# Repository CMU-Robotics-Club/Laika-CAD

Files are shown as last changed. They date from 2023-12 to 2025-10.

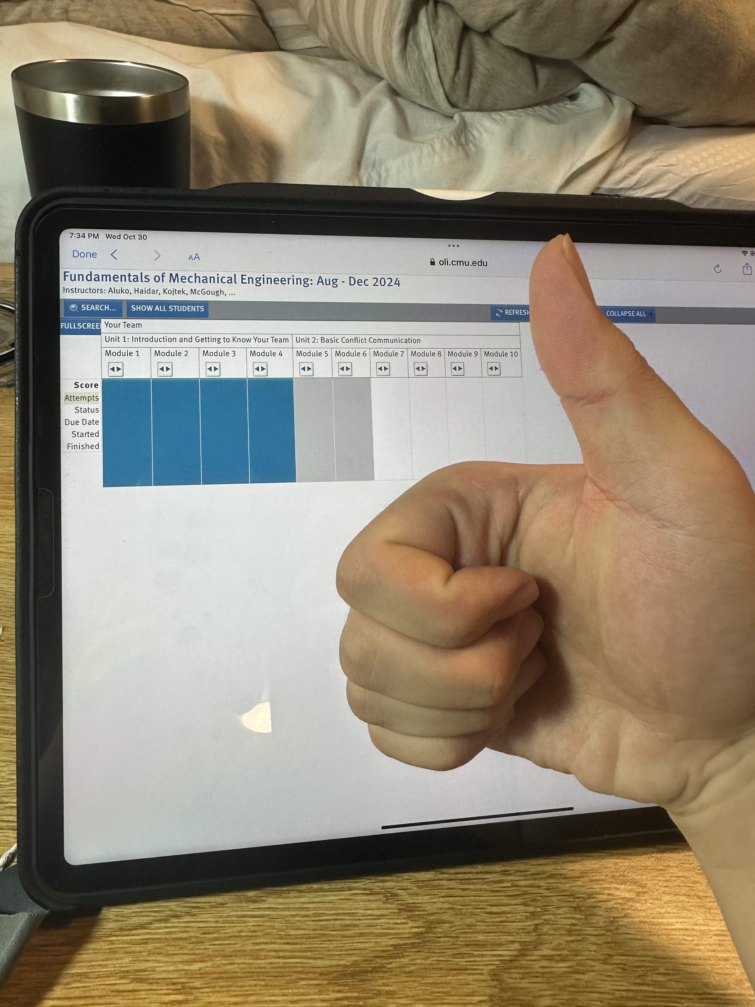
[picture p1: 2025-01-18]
LEG/IMG_3947.jpg

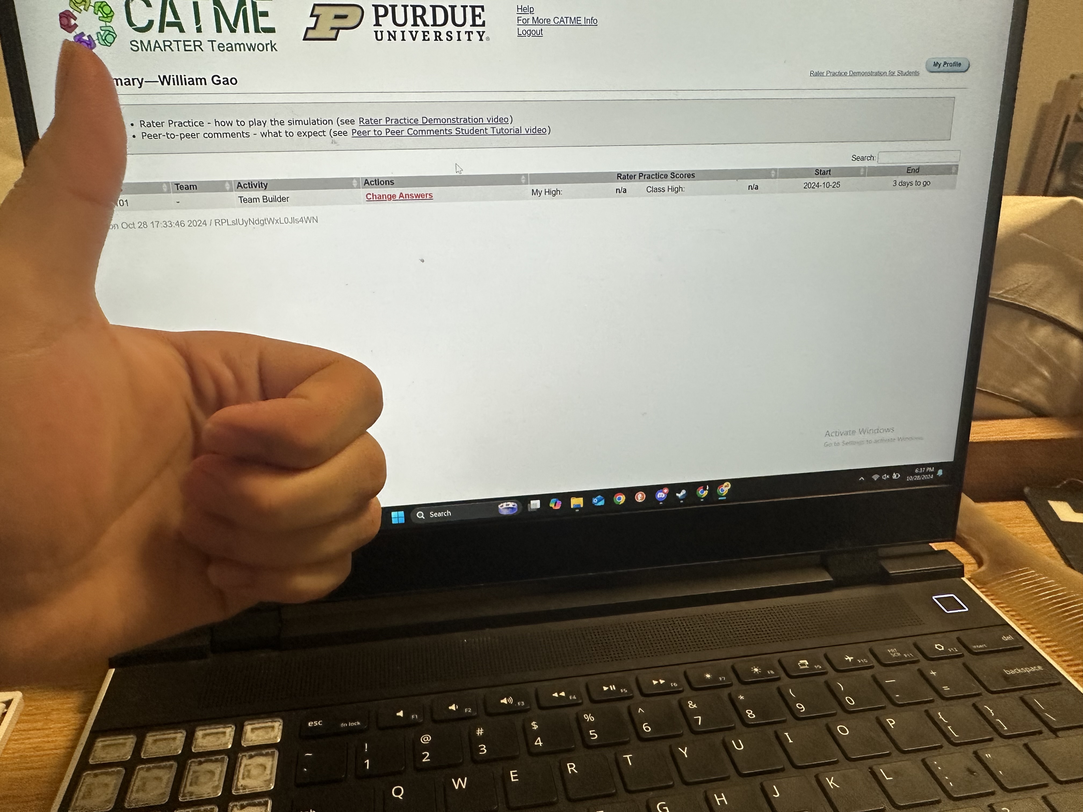
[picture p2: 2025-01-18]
LEG/IMG_3941.jpg

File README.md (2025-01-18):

# Laika-CAD
 Quadruped Project CAD Repo

## 1: Description
This repo contains all the CAD for the CMU Robotics Club Quadrupeds Project. All CAD files, whether for the robot itself, a prototype, test structures, unused designs, or anything else should live within this repo. The CAD software of choice is SOLIDWORKS; non-SOLIDWORKS files should ideally be converted when possible or clearly marked with their respective software if conversion is problematic. The overall structure follows National Robotics Engineering Center EPDM standards as detailed below.

## 2: File Locations
The top level of CAD should only contain file folders and the top-level full assembly. Folders are created for submodules (legs, drivetrain, chassis, etc.) and for component types. COTS (Commercial Off-The-Shelf) components should be identified in a COTS folder; if generic enough to have application in multiple submodules, they should live in top-level COTS. The top-level COTS includes subdirectories for component types (fasteners, bearings, etc.). If a subdirectory appropriate for a part does not exist, create one. Note that these subdirectories should have more within them (for example, a FASTENERS subdir should contain BOLTS, NUTS and NUTS should contain NYLOC, PEM, JAM) If the COTS component is highly specific, should exist in lower level COTS folder in submodule directory. Files should generally be separated by file classifiers (see below). Top-level submodule directories should only contain 900-level files and 200-level files that belong to no subassembly. 200-level files which are part of subassemblies should be organized into descriptive subdirectories. All other file levels should be organized into subdirectories within the submodule directory (e.g. a simulation for a drive train motor shaft should be within a SIMULATION folder placed in the same directory as the top-level assembly for the drive train submodule). 000, 100, 400 series files should live within MANUFACTURING, DRAWINGS, and SIMULATION folders respectively placed within the same directory as the subassembly to which the relevant parts belong to.

## 3: File Naming
### 3.1: Custom
Custom parts should obey the XXXX YZZ - NAME file number convention:  
XXX: Module ID (Alphabetical)   
Y: File type classifier (Numbers)   
ZZ: Part number (Numbers)   
NAME: Descriptive file name in Title Capitalization Form     

Example:
CYC 208 - Gearbox Mount Plate

The Module ID is an up-to-four-character code that describes the module the file belongs to. Should be as descriptive as four characters allow. The list of current module classifiers can be seen below:  
LAIK: Top-level assembly  
CHAS: Chassis  
DRIV: Drive train  
CYC: Cycloidal gearbox  
LEG: Leg design  
MTST: Motor test rig  
LTST: Leg test rig  

Please maintain this list as the project scope evolves.

The file type classifiers are as follows:  
0: Manufacturing file formats (STL, DXF, GCODE, etc.)  
1: Drawings  
2: Individual parts  
3: Equation .txt files  
4: Solidworks FEA Simulation Files  
5: Jigs/tools related to the assembly/manufacture of another part  
6: Weldments  
7: Piping, tubing, wiring, related  
8: Subassemblies  
9: Top-level assemblies. Typically no more than one (plus configurations) per module  

Please update this list as the scale of the project evolves.  

Part numbers should be defined beginning at 01. Number parts as they are created regardless of complexity, dependency, etc. Ensure that each part number for a given file type is only used once per subassembly. If you have more than 99 parts in a subassembly, you are doing something wrong!

Example:  
The completed drive train assembly would be named DRIV-901 - Drive Train Assem and would exist in the top-level DRIVE TRAIN folder.  
The housing subassembly would be DRIV-801 - Drive Train Housing and would exist in the lower-level DRIVE TRAIN/HOUSING folder.  
The drawing for one of the housing components would be DRIV-105 - Drive Train Top Cover and would exist in the DRIVE TRAIN/DRAWINGS folder.

### 3.2: COTS
COTS (Commercial Off-The-Shelf) parts should be named descriptively but do not need original part numbers. McMaster parts can be left as named when exporting as SLDPRT. Non-McMaster parts should be named descriptively, typically including part type, key dimensions, material as appropriate, etc. Additionally, should include manufacturer and part number. Use your best judgement! Someone with no project experience should be able to, from the file name, tell what the part is and where to order it.

### 3.3: Directories

Directories should be named in ALL CAPS. They should be named to describe the subassembly, component type, etc.

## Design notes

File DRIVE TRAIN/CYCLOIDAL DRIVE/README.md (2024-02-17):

# Gearbox info

Reduction: 14:1

Eccentricity: 1mm

Pin Diameter: 6mm

Pin Circle Diameter: 75mm

# List of COTS used
## Bearings
Flanged Ultra-Thin Ball Bearing with Steel Ring, Shielded, for 15 mm Shaft Diameter, 4 mm Wide - 2x
- [McMaster](https://www.mcmaster.com/4390N165/)

Flanged Ultra-Thin Ball Bearing with 440C Stainless Steel Ring, Shielded, for 10mm Shaft Diameter, 4mm Wide -2 x
- [McMaster](https://www.mcmaster.com/4390N149/)

5909K22_Needle-Roller Thrust Bearing - 1x
-  Thrust bearing with 78mm OD, 55mm ID, and 3mm Thickness
-  [McMaster](https://www.mcmaster.com/5909K22/)

1 mm Thick Washer for 55 mm Shaft Diameter Needle-Roller Thrust Bearing
-  [Mcmaster](https://www.mcmaster.com/5909k82/)

## Fasteners - this is currently misinformation
M3x14 Socket Head - 5x
- Used to fasten the load pins to rotating plate

M3 nuts - 10x
- Used to fasten the load pins to roatating plate
- Used to give threaded attachment points to the rotating plate

M3x10 Socket Head - 3x
- Used to fasten lid to main housing

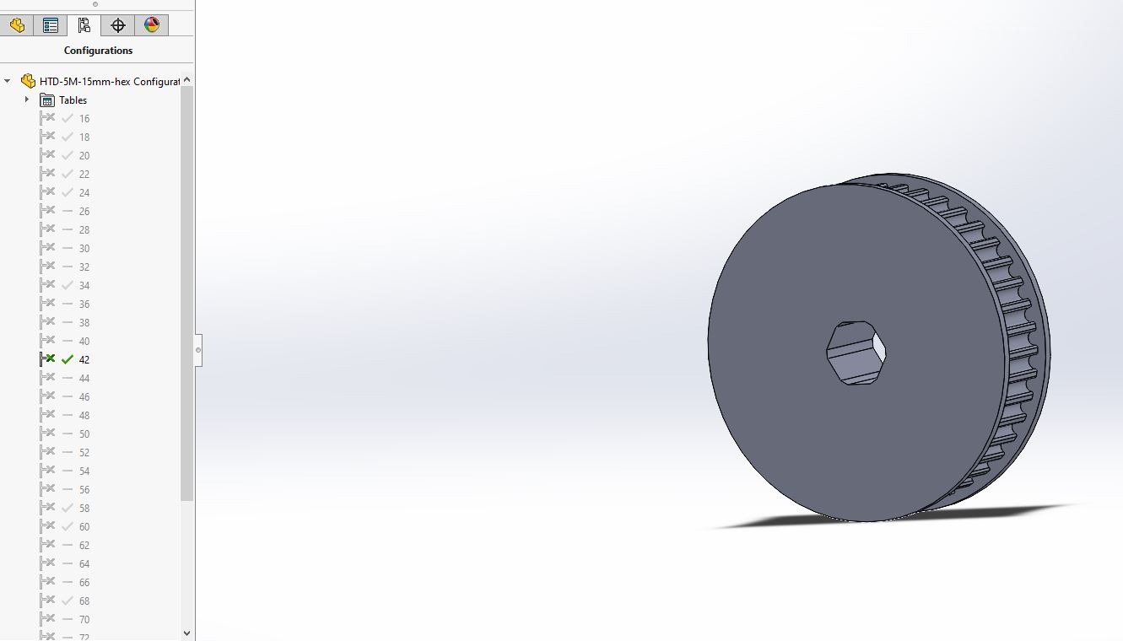
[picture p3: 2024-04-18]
PULLEY GEN/Pulley generator screenshot.JPG

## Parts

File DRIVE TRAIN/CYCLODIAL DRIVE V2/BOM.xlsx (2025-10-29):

Part Name | Description | Quantity needed per Gearbox | Total Quantitiy needed | Cost | per Unit | Total Price | Link
Shaft End Bearing | 18x12x4 Bearing | 2 | 24 | $9.99 | 10 | $29.97 | https://www.amazon.com/XIKE-6701-2RS-Bearings-12x18x4mm-Pre-Lubricated/dp/B09D2RQ4Y1
Shaft Bearing | 21x15x4 Bearing | 2 | 24 | $8.49 | 4 | $50.94 | https://www.amazon.com/uxcell-6702-2RS-Groove-Bearing-Bearings/dp/B0CNX3W3YB/ref=sr_1_11?sr=8-11
Disk Bearing | 17x9x5 | 12 | 144 | $9.99 | 10 | $149.85 | https://www.amazon.com/uxcell-9x17x5mm-Miniature-Lubricated-Bearings/dp/B0D6W6Z113/ref=sr_1_3?sr=8-3
Output Bearing | 72x55x9 | 1 | 12 | $9.99 | 2 | $59.94 | https://www.amazon.com/uxcell-6811ZZ-Groove-Bearings-Shielded/dp/B082PW8F3S/ref=sr_1_3?sr=8-3
M6 Threaded Output Pin | M6xM4x24 | 6 | 72 | $2.35 | 1 | $169.20 | https://www.mcmaster.com/97355A302/
M4 Output Pin Screws | M4 x 6mm | 6 | 72 | $7.19 | 120 | $7.19 | https://www.amazon.com/BNUOK-120pcs-Socket-Threads-Spanner/dp/B0DYS5W46C/ref=sr_1_3?sr=8-3
M3 Disk Screws | M3 x 5mm | 12 | 144 | $7.99 | 180 | $7.99 | https://www.amazon.com/BNUOK-180pcs-Socket-Threads-Spanner/dp/B0DJQGJGYT?sp_csd=d2lkZ2V0TmFtZT1zcF9hdGY
M3 Output Bearing Cover Screws | M3 x 10mm | 6 | 72 | $7.64 | 180 | $7.64 | https://a.co/d/bKohAkp
M3 Hull Screws | M3 x 50mm | 5 | 60 | $8.99 | 120 | $8.99 | https://a.co/d/6JlE1u1
Number of Gearboxes: | 12 |  |  |  | Total: | $491.71
 |  |  |  |  | Price per Gearbox: | $40.98

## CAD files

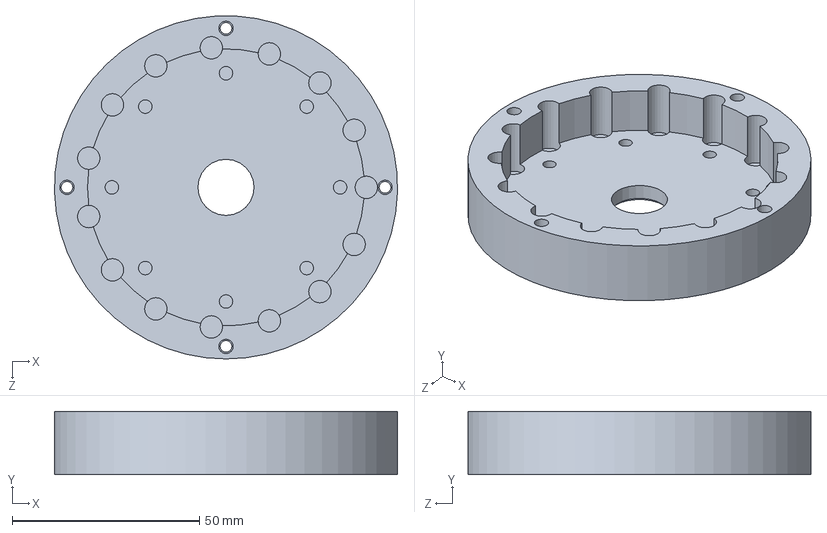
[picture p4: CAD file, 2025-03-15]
DRIVE TRAIN/CYCLOIDAL DRIVE/CYC 201 - Main Body.SLDPRT
91.7 x 16.9 x 91.6 mm

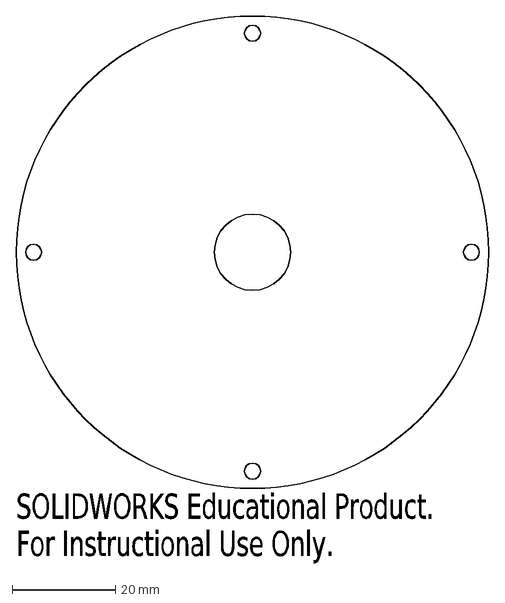
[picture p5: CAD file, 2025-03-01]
DRIVE TRAIN/CYCLOIDAL DRIVE/000 - LASER CUTTER FILES/CYC 001 - Main Body.DXF
SOLIDWORKS Educational Product.
For Instructional Use Only.

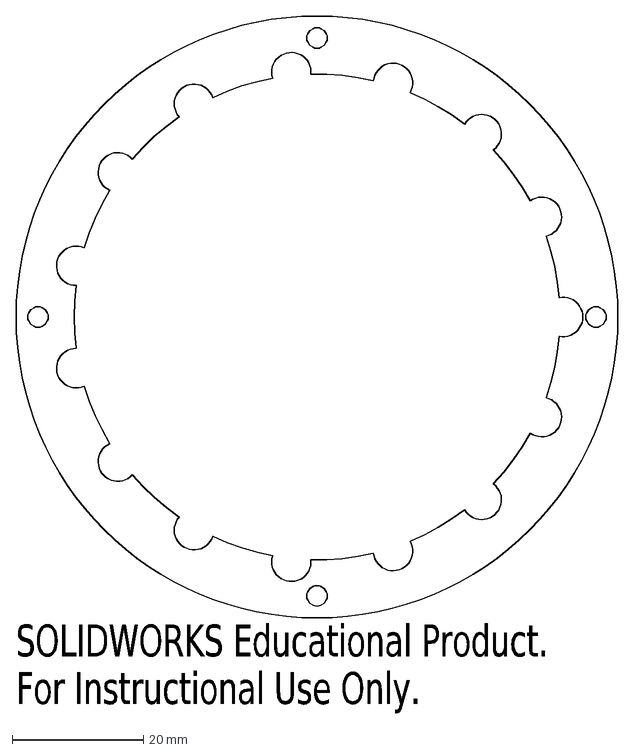
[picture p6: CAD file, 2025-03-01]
DRIVE TRAIN/CYCLOIDAL DRIVE/000 - LASER CUTTER FILES/CYC 002 - Main Body 2.DXF
SOLIDWORKS Educational Product.
For Instructional Use Only.

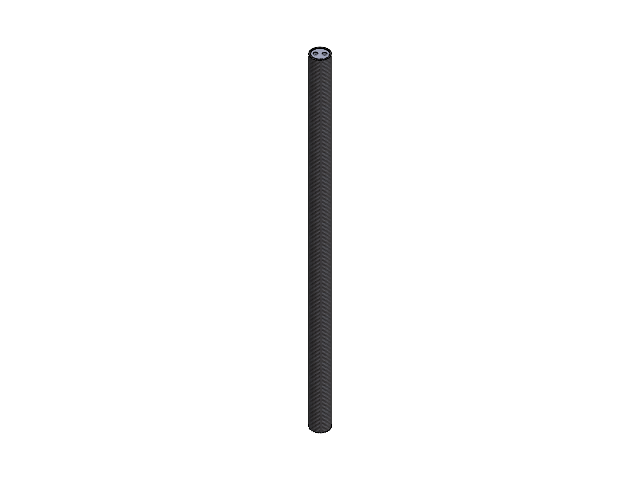
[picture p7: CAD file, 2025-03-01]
CHASSIS/CHA 804 - Middle Tube.SLDASM
CHA 202 - Middle Tube
tubePlug x 2

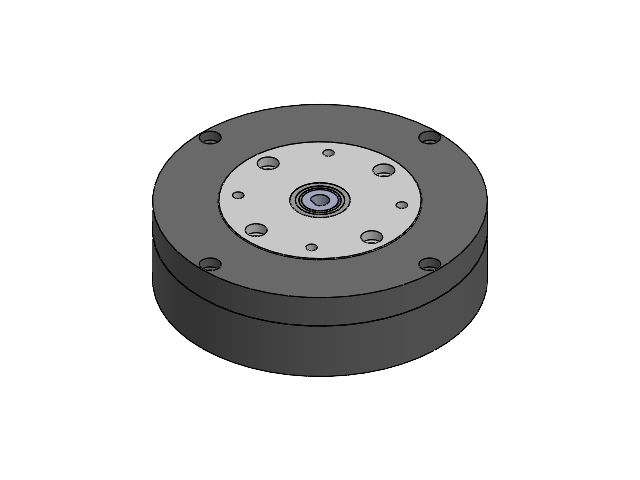
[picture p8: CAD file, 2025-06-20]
DRIVE TRAIN/CYCLOIDAL DRIVE/CYC 801 - Cycloidal Gearbox.SLDASM
CYC 205 - Eccentric Nut
CYC 204 - Eccentric Gear x 2
CYC 201 - Main Body
CYC 203 - Wall Pin x 15
CYC 207 - Top Hat
CYC 206 - Load Pin x 4
CYC 202 - Top Lid
5909K82_1 mm Thick Washer for 55 mm Shaft Diameter Needle-Roller Thrust Bearing x 2
5909K22_Needle-Roller Thrust Bearing(1)

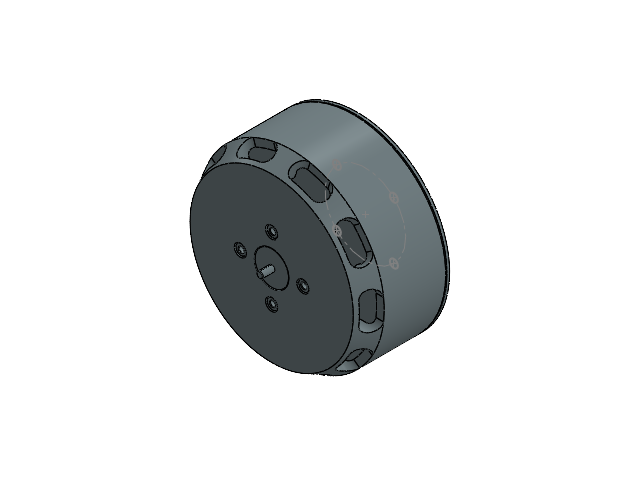
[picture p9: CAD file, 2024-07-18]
COTS - ODRIVE MOTOR/idk what all this is tbh/M8325S Motor v2.SLDASM
Magnet 5x5 Cylinder N45SH Diametrical
Saite 8325 120kv
Magnet Holder 8325 5mm

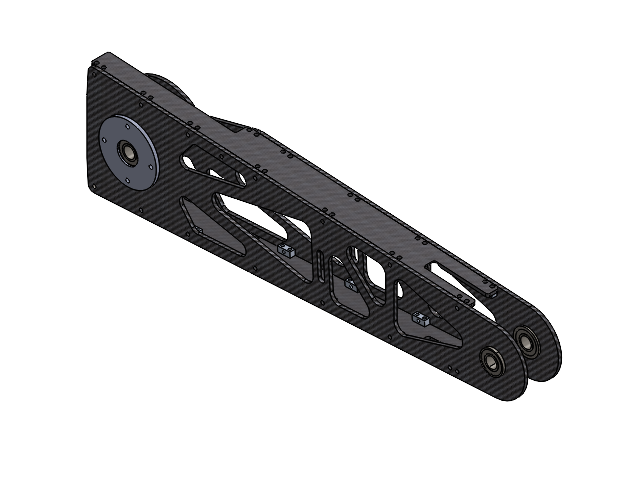
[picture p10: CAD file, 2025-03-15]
LEG/LEG 805 - Full Arm.SLDASM
LEG 213 - Arm Side Plate1
LEG 231 - LegCFSide
LEG 232 - LegCFSideDown
5mm_NutStrip_2x1_R1.1 x 25
LEG 233 - Arm Outer Plate
10.25mm Flanged Bearing.step x 3
Leg 235 - Hip Spacer
57155K629_Flanged Ball Bearing

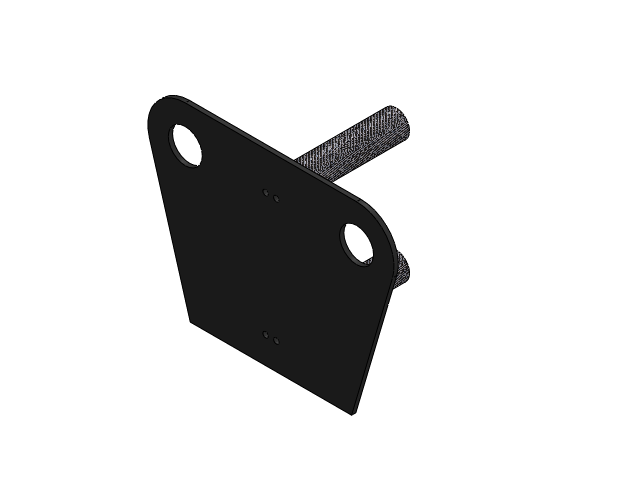
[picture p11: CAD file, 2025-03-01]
CHASSIS/CHA 802 - Front Assembly.SLDASM
CHA 203 - Front Plate
CHA 205 - Short Tube x 2
tubePlug x 4

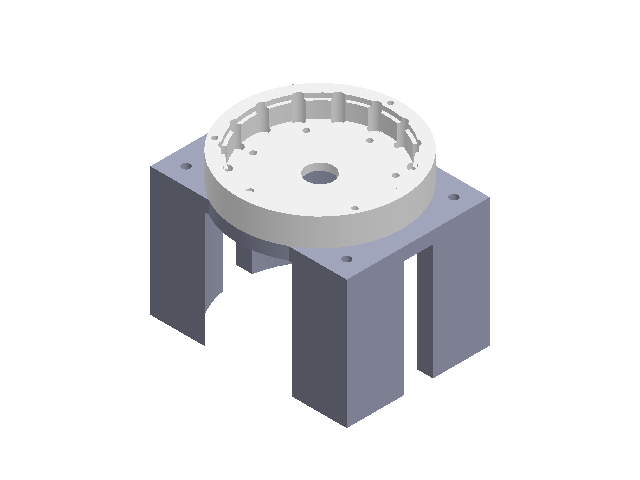
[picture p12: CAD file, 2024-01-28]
TEST RIG/GEARBOX TESTING/GTST-901 - TEST SETUP.SLDASM
GTST - 201
mainHousing

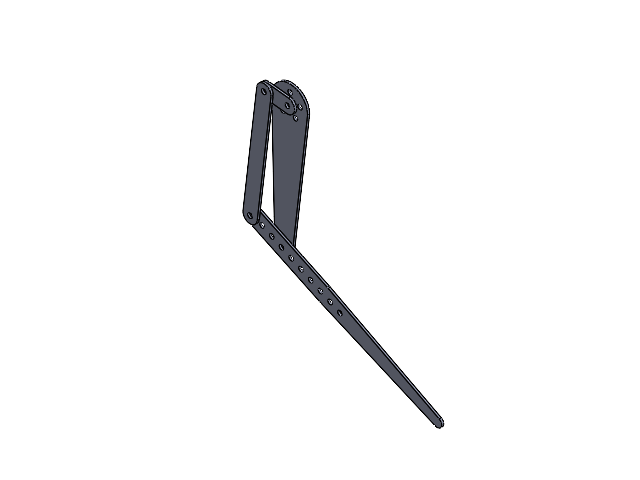
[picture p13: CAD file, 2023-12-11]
TEST RIG/LEG MODELING/LTST-901 - Test Rig.SLDASM
Upper leg
Lower leg
Shoulder flange
Tendon

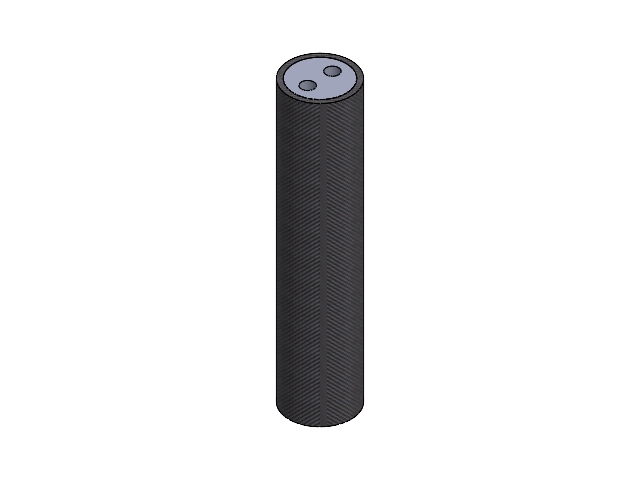
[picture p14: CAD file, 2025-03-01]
CHASSIS/CHA 805 - Short Tube.SLDASM
CHA 205 - Short Tube
tubePlug x 2

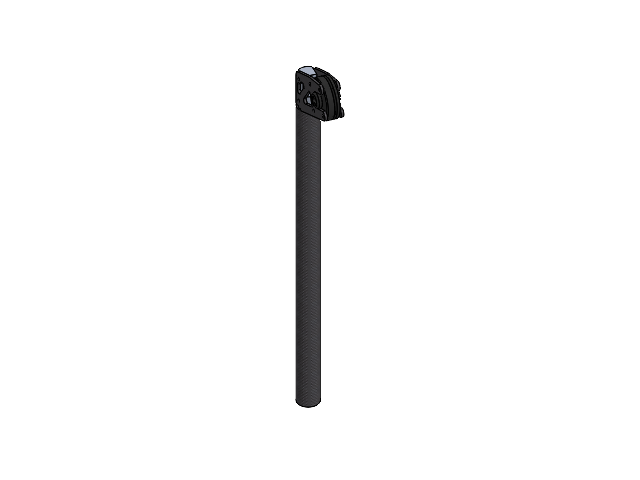
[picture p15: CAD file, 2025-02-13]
LEG/LEG 804 - Forearm.SLDASM
LEG 209 - CF Forearm Tube
LEG 210 - TubePlug
LEG 222 - CF ElbowJointSidePlate x 2
LEG 223 - Lower Forearm Sprocket Spacer
LEG 236 - Lower Forearm Sprocket Spacer Long
90576A811_Medium-Strength Steel Nylon-Insert Locknut

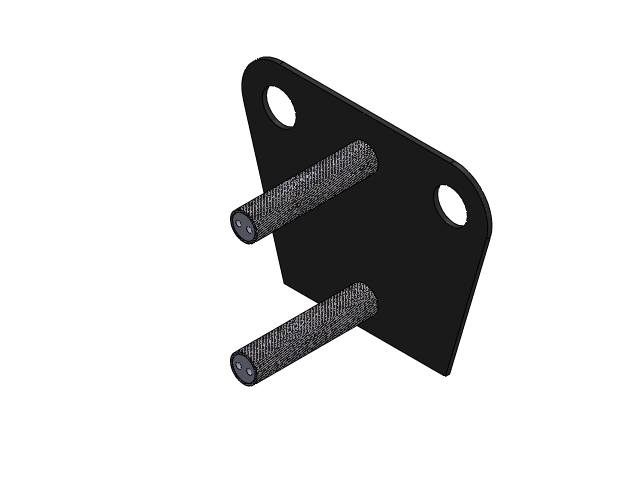
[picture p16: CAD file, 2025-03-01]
CHASSIS/CHA 803 - Back Assembly.SLDASM
CHA 204 - Back Plate
CHA 205 - Short Tube x 2
tubePlug x 4

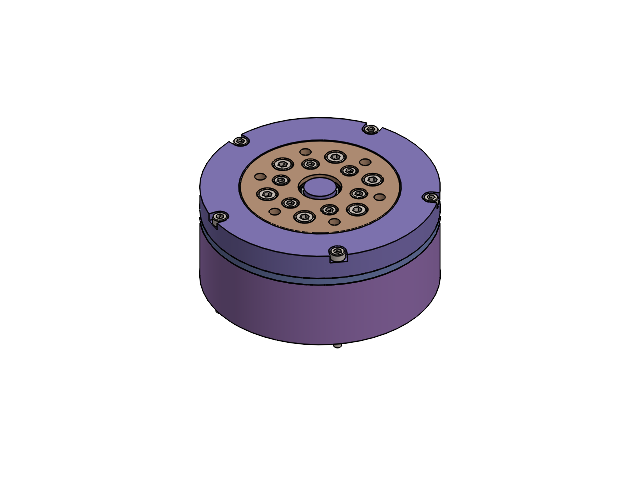
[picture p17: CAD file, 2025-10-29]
DRIVE TRAIN/CYCLODIAL DRIVE V2/CYC14 801 - Main Assembly.SLDASM
CYC14 201 - Bottom Hull
CYC14 211 - Shaft
CYC14 501 - Shaft End Bearing x 2
CYC14 221 - Bottom Disk
CYC14 502 - Shaft Bearing x 2
CYC14 503 - Disk Bearing x 12
CYC14 511 - M6 Pin x 6
CYC14 203 - Output Connector
CYC14 222 - Top Disk
socket head cap screw_am x 29
CYC14 202 - Top Hull
CYC14 204 - Top Hull Bearing Cover
CYC14 503 - Output Bearing
CYC14 205 - Output Connector Bearing Cover
CYC14 223 - Disk Cover x 2
CYC14 212 - Top Shaft Spacer
CYC14 212 - Bottom Shaft Spacer

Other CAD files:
COTS - ODRIVE MOTOR/901 - ODrive Motor Assem.SLDASM
LEG/LEG 803 - Hip Bracket.SLDASM
DRIVE TRAIN/CYCLOIDAL DRIVE/CYC 901 - Cycloidal Gearbox.SLDASM
LEG/LEG 805 - Full Armo.SLDASM
CHASSIS/CHA 201 - Middle Plate.SLDPRT
CHASSIS/CHA 202 - Middle Tube.SLDPRT
CHASSIS/CHA 203 - Front Plate.SLDPRT
CHASSIS/CHA 204 - Back Plate.SLDPRT
CHASSIS/CHA 205 - Short Tube.SLDPRT
CHASSIS/CHA 206 - Belly Pan.SLDPRT
CHASSIS/CHA 207 - Middle Support.SLDPRT
CHASSIS/CHA 208 - Battery Top Plate.SLDPRT
CHASSIS/batteryPlaceholder.SLDPRT
COTS - MCMASTER, OTHER GENERIC/BEARINGS/4473N13_Mounted Ball Bearing with Two-Bolt Flange.SLDPRT
COTS - MCMASTER, OTHER GENERIC/BEARINGS/4473N14_Mounted Ball Bearing with Two-Bolt Flange.SLDPRT
COTS - MCMASTER, OTHER GENERIC/BEARINGS/4668K214_Permanently Lubricated Stainless Steel Ball Bearing.SLDPRT
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

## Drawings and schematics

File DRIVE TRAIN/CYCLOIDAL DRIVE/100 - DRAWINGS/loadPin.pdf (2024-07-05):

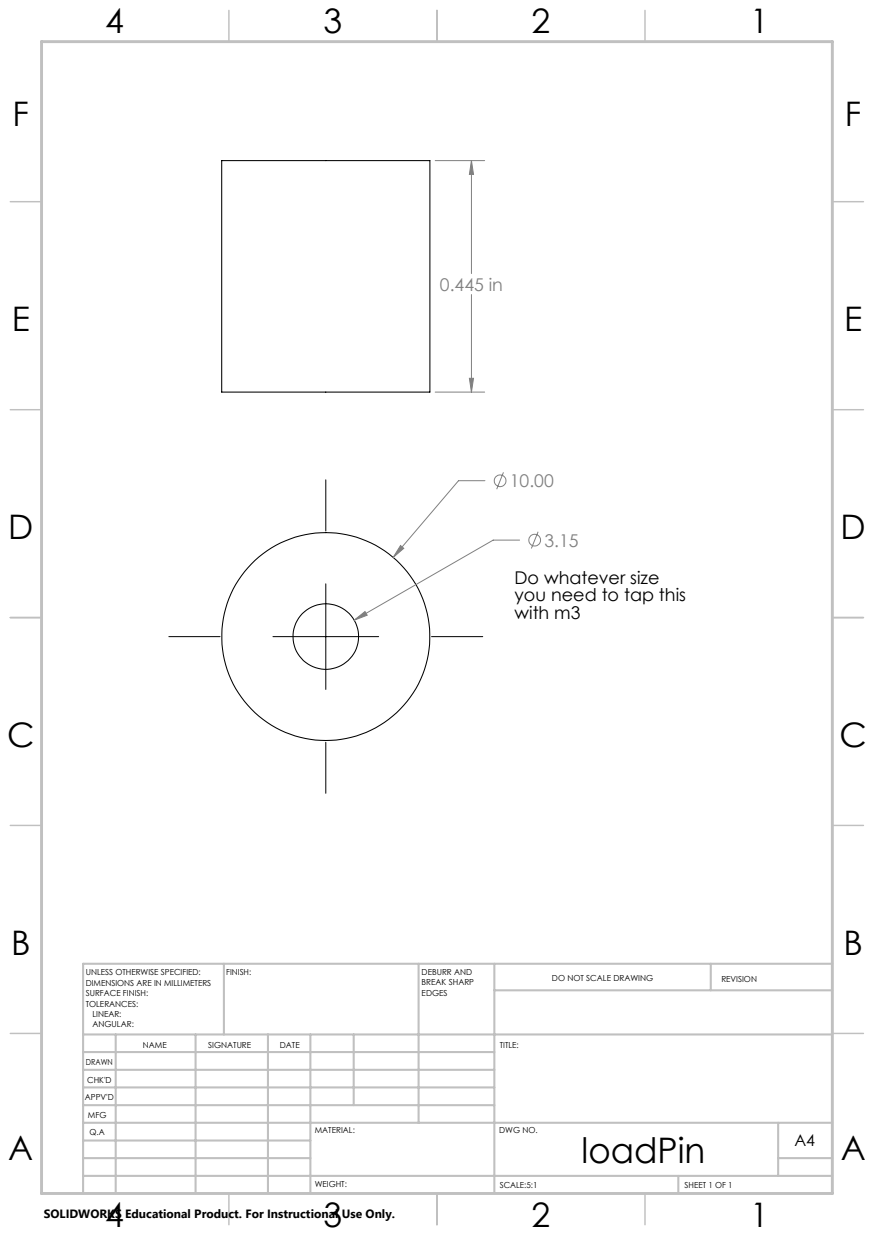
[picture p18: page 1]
FINISH:; DEBURR AND; BREAK SHARP; DO NOT SCALE DRAWING; REVISION; SCALE:5:1; SHEET 1 OF 1

Do whatever size
you need to tap this
with m3

UNLESS OTHERWISE SPECIFIED:
DIMENSIONS ARE IN MILLIMETERS
SURFACE FINISH:
TOLERANCES:
LINEAR:
ANGULAR:

NAME | SIGNATURE | DATE | | | | TITLE:

DRAWN
CHK'D
APPV'D
MFG
Q.A | | | | MATERIAL: | DWG NO. loadPin | A4

SOLIDWORKS Educational Product. For Instructional Use Only.

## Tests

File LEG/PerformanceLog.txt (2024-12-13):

Number of Contacts: 146
Number of contact data: 17712

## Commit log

2023-12-11 Initialized, added files
    Added files with NREC EPDM organization, updated readme.
    [201 - 3.8 Shaft.SLDPRT, 201 - Fan Test Stand.SLDPRT, 201 - Upper Leg.SLDPRT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]
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2023-12-12 Updated drive train design, added housing assem
    [3693N11_High-Strength HTD Timing Belt Idler Pulley.SLDPRT, 3693N14_High-Strength HTD Timing Belt Idler Pulley.SLDPRT, 60355K165_Ball Bearing.SLDPRT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]
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2023-12-28 added weird standoff thing
    [eccentricNut.sldprt]
2023-12-31 Updated files and readme
    [4668K252_Permanently Lubricated Stainless Steel Ball Bearing.SLDPRT, eccentricNut.sldprt, lid.sldprt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]
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2024-01-26 folder for solidworks made
    this is gonna be a mess for now, ill format it later
    [mainBody.SLDPRT]
2024-01-28 idk i just got dumped but heres some cad :)
    [4668K252_Permanently Lubricated Stainless Steel Ball Bearing.SLDPRT, Assem1.SLDASM, ballBearing296.SLDPRT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]
2024-01-28 i did some more stuff
    the rolly torque transmition things are missing, any screws, and the thrust bearing. also all the clearances must be found
    [4668K254_Permanently Lubricated Stainless Steel Ball Bearing.SLDPRT, Assem1.SLDASM, Disk.SLDPRT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]
2024-01-28 got rid of the nasty stuff
    [Assem1.SLDASM, Disk.SLDPRT, ballBearing296.SLDPRT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]
2024-01-28 did some sheisse idk i forgor
    [topHat.SLDPRT]
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2024-01-28 got rid of cringe
    [mainHousing.sldprt]
2024-01-30 adjusted clearances
    clearances to find left:
    - change gear clearance thing
    - ball bearing clearance (the actual balls)
    [Assem1.SLDASM, Disk.SLDPRT, ballBearing296.SLDPRT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]
2024-01-30 added colors
    see previous commit for what to do next
    [Assem1.SLDASM, mainBody.SLDPRT, topHat.SLDPRT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]
2024-01-31 did the stuf i said i woudl do
    [Assem1.SLDASM, Disk.SLDPRT, ballBearing296.SLDPRT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]
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2024-02-11 fixed some dimension stuff
    a lot is like still fucked
    [Disk.SLDPRT, eccentricNut.sldprt, loadPin.SLDPRT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]
2024-02-17 i did stuff lmao
    [(15)4390N149_Flanged Ultra-Thin Ball Bearing.SLDPRT, 4390N165_Flanged Ultra-Thin Ball Bearing.SLDPRT, 5909K22_Needle-Roller Thrust Bearing(1).SLDPRT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]
2024-02-17 pee pee poo poo
    [topLid.SLDPRT]
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2024-03-15 clearance stuff
    [Disk.DXF, Disk.SLDPRT, Disk2.DXF]
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2024-04-06 fixed leg
    [HTD-5M-15mm-hex.SLDPRT, LEG-201 - Plate.SLDPRT, LEG-202 - Motor Pulley Plate.SLDPRT]
2024-04-06 leg 2 double pulley edition
    [HTD-5M-15mm-hex.SLDPRT, LEG-201 - Plate.SLDPRT, LEG-202 - Motor Pulley Plate.SLDPRT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]
2024-04-18 i am sane and can be trusted around automobiles
    [circleShim.SLDPRT, circleShim.STEP, eccentricNut.STEP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]
2024-04-20 Add lower plate file via upload
    [LEG 203 - Lower Plate.SLDPRT]
2024-04-20 Rename LEG 203 - Lower Plate.SLDPRT to LEG 204 - Lower Plate.SLDPRT
    [LEG 204 - Lower Plate.SLDPRT]
2024-04-20 Lower leg plate files
    [LEG 204 - Lower Leg Plate.SLDPRT]
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2024-07-05 renamed stuff
    assembly is still broken
    [CYC 001 - Main Body.DXF, CYC 002 - Main Body 2.DXF, CYC 003 - Top Lid 1.DXF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]
2024-07-11 fixed equation dependency
    [eccentricNut.STL]
2024-07-18 renamed parts, also motor mount stuff
    [CYC 201 - Main Body.SLDPRT, CYC 208 - Motor Clip.SLDPRT, CYC 209 - Female Shaft Adapter.SLDPRT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]
2024-09-08 i am dumb
    asdfadgsadasfggawagregareagr
    [CYC 006 - Top Hat 1.DXF, CYC 006 - Top Hat 2.DXF, CYC 011 - topHatThin.SLDPRT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]
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2024-09-17 Knee motor mounting position change
    [CYC 201 - Main Body.SLDPRT, LEG-204 Upper Arm.SLDPRT, LEG-206 Frame.SLDPRT]
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2024-10-01 updated shaft clearance
    [CYC 209 - Female Shaft Adapter.SLDPRT]
2024-10-09 git commit whatever the fuck i did these few days idk i forgor
    [CYC 009 - Female Shaft Adapter.SLDPRT, CYC 009 - Female Shaft Adapter.STL]
2024-10-09 File Names Fixed
    [CYC 201 - Main Body.SLDPRT, LEG-209 CF Forearm Tube.SLDPRT, LEG-210 TubePlug.SLDPRT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]
2024-10-10 90degree bend added to leg joint
    [CYC 201 - Main Body.SLDPRT, LEG-212 Forearm Pulley Mount.SLDPRT, LEG-216 Forearm Pulley Mount 90degree.SLDPRT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]
2024-10-10 equations and middle plate thingy
    [CHA-201-Middle Plate.SLDPRT]
2024-10-12 Leg Spacing Fixed
    [CYC 201 - Main Body.SLDPRT, LEG-211 Forearm Pulley.SLDPRT, LEG-214 LegSheetMetalSide.SLDPRT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]
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2024-10-22 saved one (1) (I) file
    [LEG 803 - Hip Bracket.SLDASM]
2024-10-22 merged hip williaM INTO BODy danya
    [CYC 201 - Main Body.SLDPRT, CYC 209 - Female Shaft Adapter.SLDPRT, LEG 204 - Lower Leg Plate.SLDPRT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]
2024-10-23 started working more on body
    todo
    - make the position of the "holes" for motor mount on the front plate be derived from that of the middle plates
    [Assem2.SLDASM, CHA 801 - Middle Assembly.SLDASM, CHA 802 - Front Assembly.SLDASM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]
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2024-10-25 Added CF shoulder plate to main assembly
    [LEG 208 - CF Bracket Reinforcement.SLDPRT]
2024-10-25 Actually added the plates
    [CYC 201 - Main Body.SLDPRT]
2024-10-29 Added New Spacer on top
    [CYC 201 - Main Body.SLDPRT, LEG 209 - CF Forearm Tube.SLDPRT, LEG 213 - Arm Side Plate.SLDPRT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]
2024-10-30 Elbow Joint Motor Mounting Finished
    [10.25mm Flanged Bearing.step, CYC 201 - Main Body.SLDPRT, LEG 217 - Elbow Motor spacer.SLDPRT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]
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2024-11-15 Changes to the Old Assembly
    - removed rods
    - separate CF tube for bottom front and back
    [CHA 802 - Front Assembly.SLDASM, CHA 803 - Back Assembly.SLDASM, CHA-201-Middle Plate.SLDPRT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]
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2024-11-24 progress check -- all assemblies broken
    [CYC 201 - Main Body.SLDPRT, LEG 207 - Motor Bracket Bent Sheet Metal.SLDPRT, am-0233 32T 25 Chain Bearing Bore Sprocket.STEP]
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2024-11-24 Literially no idea what is going on (GOD?)
    [am-3915_25 25 Chain Inline Tensioner REV3.STEP]
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2024-12-03 Revert "driven dimension shtufff"
    This reverts commit ce57025ba4d824377ffcb4c915e27c631bb65429.
    [CHA 201 - Middle Plate.SLDPRT]
2024-12-03 idk what broke all this oy vey
    [001 clips for printing.STL, CHA-201-Middle Plate.SLDPRT, CHAS 202 - CarbonFiberClip.SLDPRT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]
2024-12-03 removed bottom tube, made front and back plates shorter
    [CHA 201 - Middle Plate.SLDPRT, CHA 202 - Middle Tube.SLDPRT, CHA 203 - Bottom Tube.SLDPRT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]
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2024-12-13 changed holes for cf tubes and added plug
    [CHA 201 - Middle Plate.SLDPRT, CHA 202 - Middle Tube.SLDPRT, CHA 203 - Front Plate.SLDPRT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]
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2024-12-13 made temporary assembly to see how legs look w chassis
    [CHA 201 - Middle Plate.SLDPRT, CHA 202 - Middle Tube.SLDPRT, CHA 203 - Front Plate.SLDPRT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]
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2024-12-19 Mount holes for guards and box mount for mature
    [(15)4390N149_Flanged Ultra-Thin Ball Bearing.SLDPRT, 4390N165_Flanged Ultra-Thin Ball Bearing.SLDPRT, 5909K22_Needle-Roller Thrust Bearing(1).SLDPRT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]
2024-12-19 mount bracket holes spacing fixed
    [5909K22_Needle-Roller Thrust Bearing(1).SLDPRT, 5mm_NutStrip_2x1_R1.1.SLDPRT, 8325 with Magnet - Saite 8325 120kv.SLDPRT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]
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2024-12-26 Forarm Endstop added, interference fixed
    [4390N165_Flanged Ultra-Thin Ball Bearing.SLDPRT, 5909K22_Needle-Roller Thrust Bearing(1).SLDPRT, 5mm_NutStrip_2x1_R1.1.SLDPRT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]
2024-12-29 gearbox updates
    need to fix spacing between gears and thrust bearing, also increase length of output
    [CYC 001 - Main Body.DXF, CYC 002 - Main Body 2.DXF, CYC 201 - Main Body.SLDPRT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]
2024-12-30 Tube plug fixed, bottom odrive flipped, top sprocket spacer modified
    [(15)4390N149_Flanged Ultra-Thin Ball Bearing.SLDPRT, 4390N165_Flanged Ultra-Thin Ball Bearing.SLDPRT, 5909K22_Needle-Roller Thrust Bearing(1).SLDPRT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]
2024-12-31 todo list half done
    TPU foot, Bottom Odrive Flipped, motor mounting redone
    [(15)4390N149_Flanged Ultra-Thin Ball Bearing.SLDPRT, 5909K22_Needle-Roller Thrust Bearing(1).SLDPRT, 5mm_NutStrip_2x1_R1.1.SLDPRT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]
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2025-01-09 Fixed Limit switch constraints
    [57155K629_Flanged Ball Bearing.SLDPRT, 5909K22_Needle-Roller Thrust Bearing(1).SLDPRT, 80x80x38 Fan.SLDPRT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]
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2025-01-18 Fixed Merge with leg-static-knee-motor
    [CYC 201 - Main Body.SLDPRT, CYC 210 - Plates Standoff Tube.SLDPRT, LEG 207 - Motor Bracket Bent Sheet Metal.SLDPRT]
2025-02-13 Clearance and tolerance fixes to spacers
    [90576A102_Medium-Strength Steel Nylon-Insert Locknut.SLDPRT, CYC 201 - Main Body.SLDPRT, LEG 207 - Motor Bracket Bent Sheet Metal.SLDPRT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]
2025-02-19 stuff
    i made this bc solidworks is greedy and makes their software unuseable because money
    [CYC 204 - Eccentric Gear.SLDPRT]
2025-02-19 fixing stuff
    [(15)4390N149_Flanged Ultra-Thin Ball Bearing.SLDPRT, 4390N165_Flanged Ultra-Thin Ball Bearing.SLDPRT, Ball Bearing Ball - 3.5mm.SLDPRT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]
2025-02-19 reversing some 2025 damage
    [CYC 204 - Eccentric Gear.SLDPRT, CYC 205 - Eccentric Nut.sldprt]
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2025-03-01 Fixed faulty Sprocket Guard Geometry
    [CYC 201 - Main Body.SLDPRT, LEG 237 - Lower Chain Guard.SLDPRT]
2025-03-15 Updated Knee Motor Cover for new gearbox mounts and limit switch
    [91290A017_Alloy Steel Socket Head Screw.SLDPRT, CYC 201 - Main Body.SLDPRT, CYC 202 - Top Lid.SLDPRT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]
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2025-06-20 Revert "more mature parts"
    This reverts commit 7416bf9d5b08666f80eef6642ade20d691233d97.
    [CYC 201 - Main Body.SLDPRT, CYC 202 - Top Lid.SLDPRT, CYC 204 - Eccentric Gear.SLDPRT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]
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
